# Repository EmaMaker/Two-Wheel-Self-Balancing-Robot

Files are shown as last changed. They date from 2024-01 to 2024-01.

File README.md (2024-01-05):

# Two-wheeled Self-Balancing Robot

My attempt at building a two-wheeled self-balancing robot. The project started as a personal one and
later evolved as a University project. I'll upload the university report to this repo as soon as it is complete. This repo will also be
supported by a blog post on [emamaker.com](https://emamaker.com)

The physical model of the robot has been derived by calculating the Lagrangian function. This model
is heavily non-linear and has been linearized around the 0° point of equilibrium.

The linearized model has been reconstructed in MatLab Simulink and a discrete-time PID controller
has been calculated by trial and error. This PID Controller was used to dimension the motors (max. torque
	in particular) and was later refined with the Ziegler-Nichols method.

The robot has later been built using a Raspberry Pi Pico microcontroller paired with a MPU6050
6-axis IMU, from which the pitch angle is derived with the use of a [Madgwick](https://ahrs.readthedocs.io/en/latest/filters/madgwick.html) filter.
(Initially this was a simple complementary filter, but it was way too subject to noise from the
 accelerometer, check the blog post).
The two motors (Hitec HS-322HD servomotors, check blog post for the choice
     of motors) are driven by a L298N motor driver. Everything is powered by a 2S 7.4V LiPo battery.

The microcontroller firmware has been implemented in Arduino-C with the use of the ArduPID library
 for the PID Controller and FastIMU for reading the IMU. A reimplementation using the RPi Pico own
 SDK will probably follow. This repo includes both the old firmware using a complementary filter and
 the new one using the Madgwick filter, the latter is the one actually used on the robot.

The structure (as in chassis) of the robot has been designed in OnShape and realized using laser-cut
wood and 3d-printed parts, check the blog post for details about the structure.

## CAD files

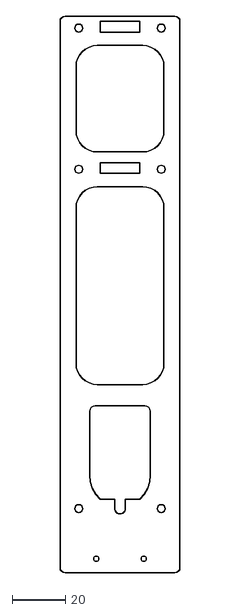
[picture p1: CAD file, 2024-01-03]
structure/sbr-side-v2.dxf
45.0 x 209.0

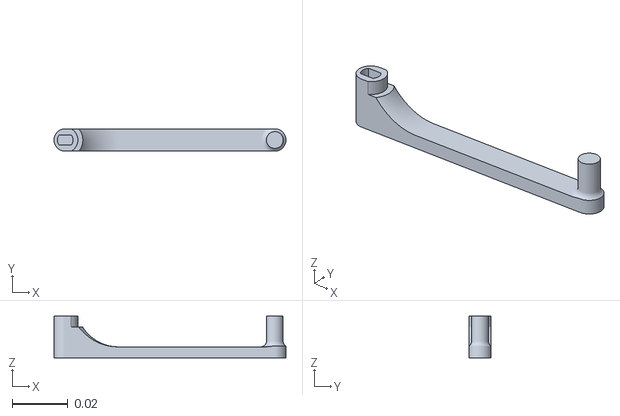
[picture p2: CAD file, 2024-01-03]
torque-measure-arm.stl
0.083 x 0.008 x 0.015

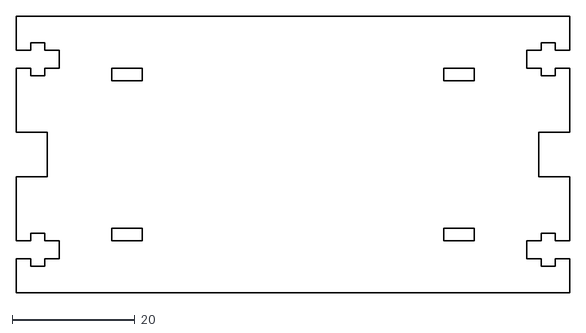
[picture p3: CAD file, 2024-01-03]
structure/sbr-motor-holder.dxf
90.0 x 45.0

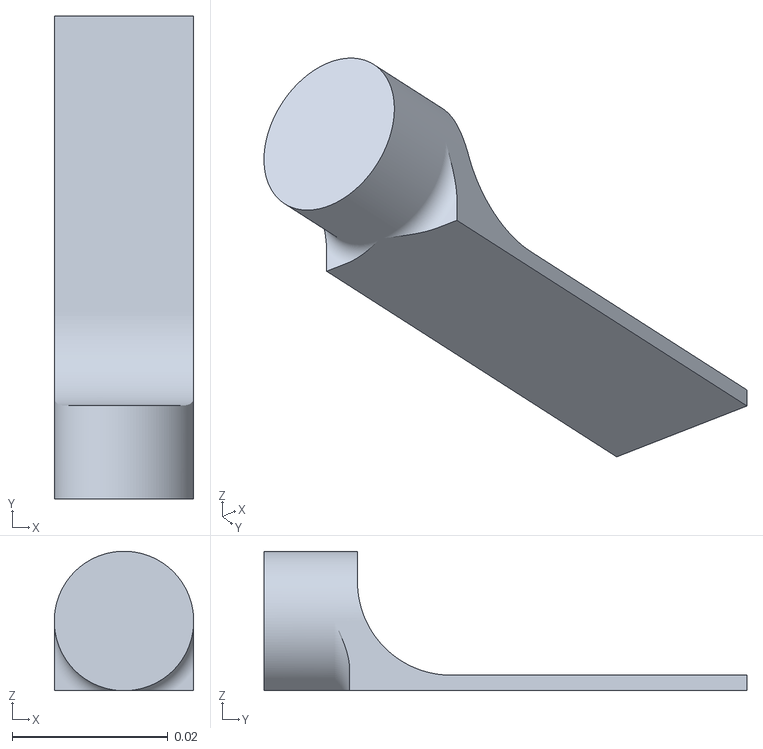
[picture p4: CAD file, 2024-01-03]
torque-measure-dynamometer.stl
0.0179 x 0.062 x 0.0179

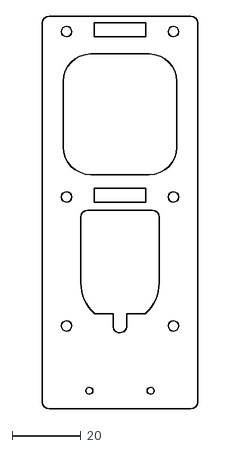
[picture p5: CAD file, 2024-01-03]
structure/sbr-side-short.dxf
45.0 x 114.0

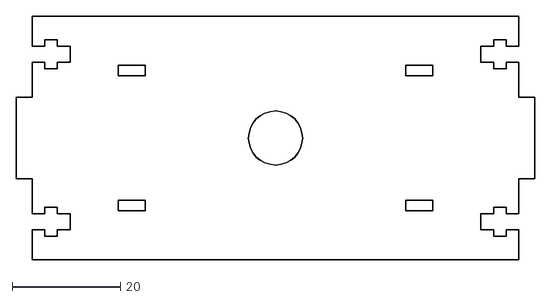
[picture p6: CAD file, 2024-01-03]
structure/sbr-motdrv.dxf
96.0 x 45.0

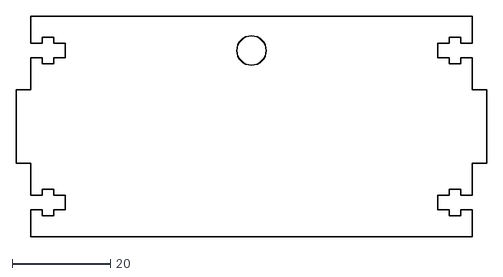
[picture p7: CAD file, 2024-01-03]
structure/sbr-uc.dxf
96.0 x 45.0

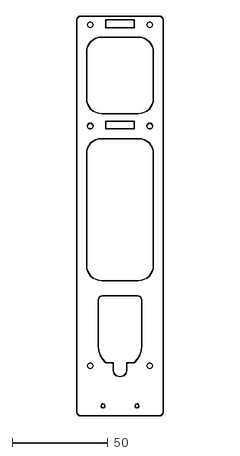
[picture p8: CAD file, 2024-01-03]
structure/sbr-side.dxf
45.0 x 209.0

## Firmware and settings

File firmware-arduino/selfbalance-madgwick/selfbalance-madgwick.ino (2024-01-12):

#include <ArduPID.h>

#define MOT_DX 0
#define MOT_SX 1

constexpr float MOT_SX_MULT = 1.0;
constexpr float MOT_DX_MULT = 1.0;

ArduPID myController;

// Calculated with matlab, then adjusted by hand

/* With KP = 10, about  12 periods of oscillation in 1sec
Pc = 0.083

PID Kp = 0.6Kc, Ti = 0.5Pc Td = 0.125Pc
Ki = KpTc/ti
Kd = KpTd/Tc
*/ 


constexpr double KP = 5.8;
constexpr double KI = 0.2;
constexpr double KD = 0.1;

//double setpoint = -0.015;
double setpoint = 0.0;
double output = 0;
double input = 0;

double roll{ 0 }, pitch{ 0 }, yaw{ 0 };

constexpr double max_torque_sx = 0.392;
constexpr double max_torque_dx = 0.36;
constexpr double max_torque = max_torque_dx+max_torque_sx;
constexpr double torque_sx_coeff = max_torque_sx/max_torque;
constexpr double torque_dx_coeff = max_torque_dx/max_torque;

void setup(void) {
  Serial.begin(9600);
  delay(500);

  setup_imu();
  setup_motors();
 
  pinMode(LED_BUILTIN, OUTPUT);
  digitalWrite(LED_BUILTIN, HIGH);

  // Let the initial error from madgwick filter discharge without affecting the integral term of the PID
  unsigned long t = millis();
  while (millis() - t < 3000) {
    update_imu();
  }

  myController.begin(&input, &output, &setpoint, KP, KI, KD, P_ON_E, FORWARD);
  myController.setOutputLimits(-max_torque, max_torque);  // double of max torque motors can exhert
  // myController.setWindUpLimits(-0.2 , 0.02);
  myController.setSampleTime(1);
  myController.start();


  digitalWrite(LED_BUILTIN, LOW);
}

double map_double(double x, double in_min, double in_max, double out_min, double out_max) {
  return (x - in_min) * (out_max - out_min) / (in_max - in_min) + out_min;
}

void loop() {
  compute();
}

void compute(){
  update_imu();

  input = pitch;

  myController.compute();

  double torque = abs(output);

  double s = sign(output);
  double pwm_dx = torque <= 0.005 ? 30*s : torque_to_pwm_dx(torque*torque_dx_coeff)*s;
  double pwm_sx = torque <= 0.005 ? 30*s : torque_to_pwm_sx(torque*torque_sx_coeff)*s;

  move_pwm(MOT_SX, pwm_sx);
  move_pwm(MOT_DX, pwm_dx);
}

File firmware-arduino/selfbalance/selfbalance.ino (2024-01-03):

#include <ArduPID.h>

#define MOT_DX 0
#define MOT_SX 1

constexpr float MOT_SX_MULT = 1.0;
constexpr float MOT_DX_MULT = 1.0;

ArduPID myController;

// Calculated with matlab
constexpr double KP = 1;
constexpr double KI = 0.02;
constexpr double KD = 0.05;

double setpoint = 0;
double output = 0;
double input = 0;

double setpoint_front = 0;
double output_front;

double angleX{0}, angleY{0}, angleZ{0};
double angAccX{0}, angAccY{0};
double accX{0}, accY{0};

void setup(void) {
  Serial.begin(9600);
  delay(500);
  
  setup_imu(5);;
  Serial.println("IMU up");
  setup_motors();
  Serial.println("Motors up");
  
  pinMode(LED_BUILTIN, OUTPUT);
  digitalWrite(LED_BUILTIN, HIGH);

  delay(200);
   
  myController.begin(&input, &output, &setpoint, KP, KI, KD, P_ON_E, FORWARD);
  myController.setOutputLimits(-0.4, 0.4); // max torque motors can exhert
  myController.setSampleTime(2);
  myController.start();

  delay(200);
  digitalWrite(LED_BUILTIN, LOW);

  test_motors_torque(1);
  /*frontController.begin(&angleZ, &output_front, &setpoint_front, 100, 0, 1, P_ON_E, FORWARD);
  frontController.setOutputLimits(-100,100);  
  myController.setWindUpLimits(-PI, PI);
  frontController.setSampleTime(1);
  frontController.start();*/

}

double map_double(double x, double in_min, double in_max, double out_min, double out_max) {
  return (x - in_min) * (out_max - out_min) / (in_max - in_min) + out_min;
}

unsigned long t = 0;
double oldpwm = 0;

void loop(){
  computeAngles();

  //static double oldAngleY = 0;
  //oldAngleY = 0.99 * oldAngleY + 0.01 * angleY;
  input = angleY;
  
  
  myController.compute();

  double torque = abs(output) * 0.5;
  double pwm = map_double(torque, 0, 0.2, 80, 255);
  pwm *= sign(output);

  Serial.println("input\toutput\ttorque\tpwm");
  Serial.print(input, 6);
  Serial.print("\t");
  Serial.print(output, 6);
  Serial.print("\t");
  Serial.print(torque);
  Serial.print("\t");
  Serial.println(pwm);
  
  move_pwm(MOT_SX, pwm*MOT_SX_MULT);
  move_pwm(MOT_DX, pwm*MOT_DX_MULT);

  oldpwm = pwm;
}

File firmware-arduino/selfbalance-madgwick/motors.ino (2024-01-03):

int mot_pins[][3] = {
  {17, 16, 20},
  {19, 18, 21}
};


// PWM value at which the motors start moving (empirical)
constexpr int base_pwm = 100  ; // Actually starts moving at 70
// Max PWM value
constexpr int max_pwm = 255;

void setup_motors(){
  pinMode(mot_pins[0][0], OUTPUT);
  pinMode(mot_pins[0][1], OUTPUT);
  pinMode(mot_pins[1][0], OUTPUT);
  pinMode(mot_pins[1][1], OUTPUT);

  Serial.println("Motors up");
}

double torque_to_pwm_sx(double t){
  return 547.323 * t + 50.874;
}

double torque_to_pwm_dx(double t){
  return 684.284 * t + 44.29;
}

double speed_to_pwm(double speed){
  return map(speed, 0, 100, 0, 255);
}

int sign(auto b){
  return b == 0 ? 0 : b > 0 ? 1 : -1;
}

void move(int mot, double speed){
  double pwm = speed_to_pwm(speed);
  move_pwm(mot, pwm*sign(speed));
}

void move_pwm(int mot, int pwm){
  if(pwm == 0){
    digitalWrite(mot_pins[mot][0], LOW);
    digitalWrite(mot_pins[mot][1], LOW);
  }else if(pwm < 0){
    digitalWrite(mot_pins[mot][0], HIGH);
    digitalWrite(mot_pins[mot][1], LOW);
  }else{
    digitalWrite(mot_pins[mot][1], HIGH);
    digitalWrite(mot_pins[mot][0], LOW);
  }

  analogWrite(mot_pins[mot][2], abs(pwm));
}

void test_motors(){
  while(!Serial) delay(10);

  int m = 0;
  while(true){
    digitalWrite(mot_pins[m][0], LOW);
    digitalWrite(mot_pins[m][1], HIGH);
    
    for(int i = 0; i < 255; i++){
      Serial.print("PWM: ");
      Serial.println(i);
      analogWrite(mot_pins[m][2], i);
      delay(100);
    }
    delay(1000);
    digitalWrite(mot_pins[m][0], LOW);
    digitalWrite(mot_pins[m][1], LOW);
    m = 1-m;
  }
}

void test_motors_nodeadzone(){
  int m = 0;
  while(true){
    for(int i = 0; i < 100; i++){
      Serial.print("Speed: ");
      Serial.println(i);
      move(m, i);
      delay(100);
    }
    delay(1000);
    move(m, 0);
    m = 1-m;
  }
}

void test_motors_rpm(){
  while(!Serial) delay(10);

  unsigned long tstart = millis();
  while(millis() - tstart < 200) {
  move(0, 20);
  }
  move(0,0);
}

void test_motors_diff(){
  move(MOT_SX, 50*MOT_SX_MULT);
  move(MOT_DX, 50*MOT_DX_MULT);
}


void test_motors_torque(int motor, int dir){
  while(!Serial){;}
  
  while(1){
    delay(1000);
    Serial.println("Setup, waiting 8 secs");
    delay(8000);
    
  for(int i = 0; i <= 255; i+= 15){
    digitalWrite(mot_pins[motor][1], dir > 0 ? LOW : HIGH);
    digitalWrite(mot_pins[motor][0], dir > 0 ? HIGH : LOW);
    Serial.print("PWM: ");
    Serial.println(i);

    analogWrite(mot_pins[motor][2], i);
    delay(8000);
    
    digitalWrite(mot_pins[motor][0], LOW);
    digitalWrite(mot_pins[motor][1], LOW);
    delay(2000);
    
    }
  }
}

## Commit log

2024-01-03 [DO NOT USE] firmware with complementary filter
2024-01-03 firmware using madgwick filter
2024-01-03 parts and data on torque of the motors
    [torque-measure-arm.stl, torque-measure-dynamometer.stl, torque-servos.ods]
2024-01-03 robot chassis
    [sbr-motdrv.dxf, sbr-motor-holder.dxf, sbr-side-short.dxf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]
2024-01-05 initial discharge of madwick filter
2024-01-05 pid: recalibrate with ziegler-nichols2 and matlab simulation
2024-01-05 pid: eyeballed for a fully charged battery
    Made a video showing the result. Apparently the center of mass is not exactly at the center of the
    robot and the battery needs to stick out a bit at the front to rebalance it.
    Also my desk is a bit tilted so the pitch is heavily affected by the yaw, the video shows it
    clearly. Next step: a inner control loop for the yaw.
2024-01-12 Revert "pid: eyeballed for a fully charged battery"
    This reverts commit 23e63c7625cd3b443a7f6ba8ec684b9a4b058475.
    [selfbalance-madgwick.ino]
2024-01-12 [UNSURE] open-loop wheel sync
2024-01-13 sim: let matlab derive transfer function
    and recalibrate pid with that
2024-01-13 sim: nonlinear simulation
    Demonstrates both the analytical solution and the current PID values work
